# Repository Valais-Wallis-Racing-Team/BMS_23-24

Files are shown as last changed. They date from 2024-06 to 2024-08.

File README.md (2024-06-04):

# foxBMS

> **_NOTE:_**
> - This is the repository of the **first generation** of foxBMS
>   (https://github.com/foxBMS/foxbms)
> - The **second generation** of foxBMS (foxBMS 2) is also found on Github
>   (https://github.com/foxBMS/foxbms-2)

foxBMS is a free, open and flexible development environment to design battery
management systems. It is the first modular open source BMS development
platform.

## Documentation

A current build of the documentation of this project can be found
here:
- [latest documentation build (of the most recent release)](https://iisb-foxbms.iisb.fraunhofer.de/foxbms/gen1/docs/html/latest/)
- [list of all available documentation builds](https://iisb-foxbms.iisb.fraunhofer.de/foxbms/gen1/docs/html/)

## Changelog

The project changelog is found in
[CHANGELOG.rst](./CHANGELOG.rst).

## License

The license information of the project is found in [LICENSE.md](./LICENSE.md).

Basically, the software is covered by the
[**BSD 3-Clause License (SPDX short identifier: BSD-3-Clause)**](https://opensource.org/licenses/BSD-3-Clause)
and the hardware and documentation by the
[**Creative Commons Attribution 4.0 International License (SPDX short identifier: CC-BY-4.0)**](https://creativecommons.org/licenses/by/4.0/legalcode).

## Acknowledgment

For funding acknowledgements and instructions on how to acknowledge foxBMS
please see [foxbms.org/acknowledgements](https://foxbms.org/acknowledgements/).

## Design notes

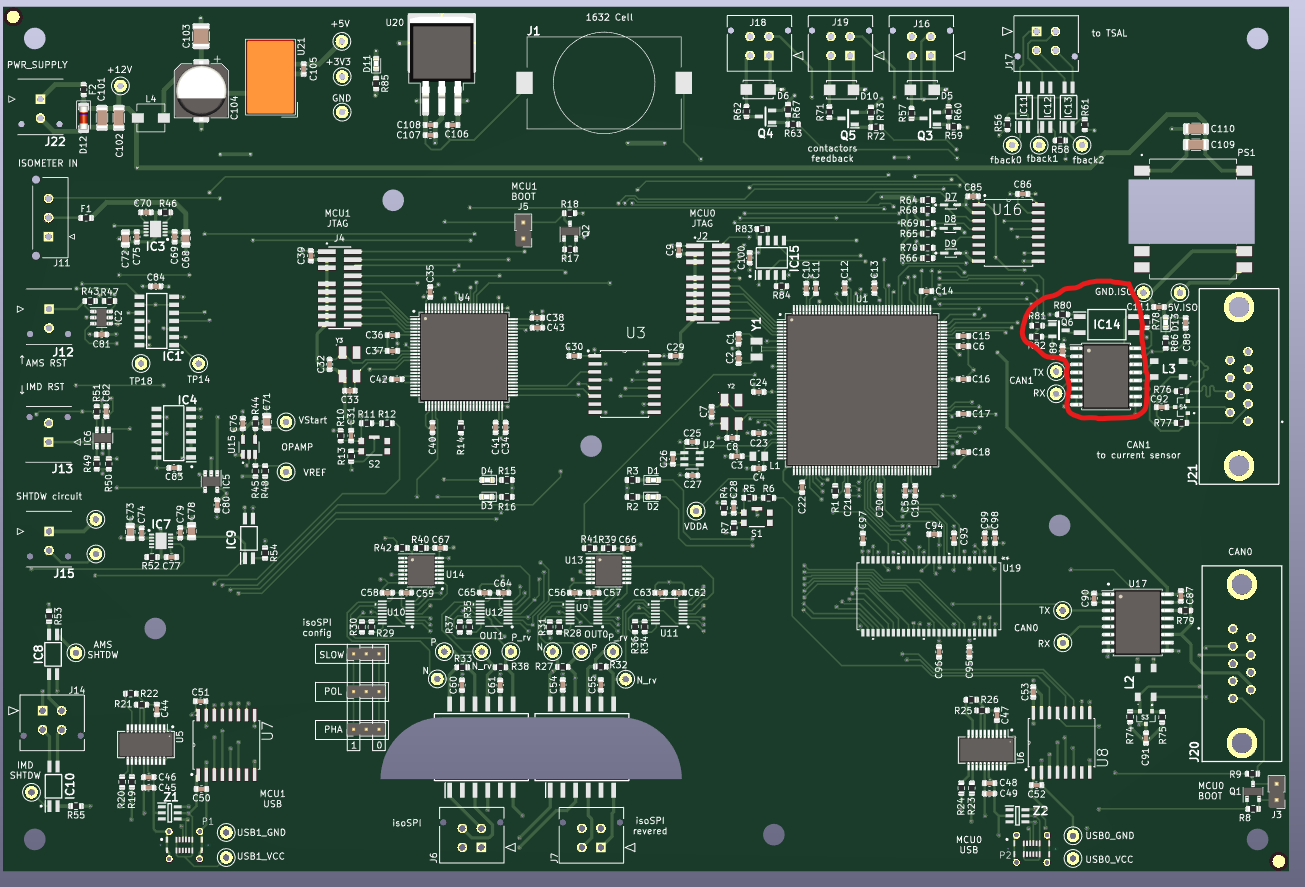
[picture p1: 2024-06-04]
hardware_KI_CAD/BMS-Master/BMS-MasterV1.1/BMS-Master_V1.0/conformal_coating_placement.png

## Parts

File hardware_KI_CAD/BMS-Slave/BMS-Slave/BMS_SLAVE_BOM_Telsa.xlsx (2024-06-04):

Fournisseur | Nbr. | N° article | Référence | Valeur | Empreinte | Description | Fitted (X) | Generic (X) | Through-hole (X) | prix unitaire | prix total
BOM BMS-Slave |  |  |  |  |  |  |  |  |  | Liste actualisée le : 12.01.2024
Composants électriques et électroniques
 | 12 | generic | C1-C3, C8-C10, C70-C72, C104-C106 | 1uF/50V | Capacitor_SMD:C_0805_2012Metric | Capa 1uF/50V | X | X |  |  | 0.00 CHF
 | 16 | generic | C4, C11, C17, C43, C53, C68, C73, C79, C107, C114, C116, C126, C139-C142 | 100nF/50V | Capacitor_SMD:C_0603_1608Metric | Capa 100nF/50V | X | X |  |  | 0.00 CHF
 | 4 | generic | C5, C12, C74, C108 | 100nF/200V | Capacitor_SMD:C_1206_3216Metric | Capa 100nF/200V | X | X |  |  | 0.00 CHF
 | 8 | generic | C6, C7, C13, C14, C75, C76, C109, C110 | 100pF/50V | Capacitor_SMD:C_0603_1608Metric | Capa 100pF/50V | X | X |  |  | 0.00 CHF
Mouser | 4 | 80-EDH336M100A9MAA | C15, C66, C77, C112 | 33uF/100V | Capacitor_SMD:CP_Elec_8x10 | Capa électrolitique 33uF/100V | X |  |  | 0.61 | 2.44 CHF
 | 4 | generic | C16, C67, C78, C113 | 2.2uF/100V | Capacitor_SMD:C_1210_3225Metric | Capa 2.2uF/100V | X | X |  |  | 0.00 CHF
 | 84 | generic | C18-C41, C44-C51, C54-C61, C64, C65, C80-C103, C117-C124, C127-C134, C137, C138 | 10nF/100V | Capacitor_SMD:C_0603_1608Metric | Capa 10nF/100V | X | X |  |  | 0.00 CHF
 | 12 | generic | C42, C52, C62, C63, C115, C125, C135, C136, C143-C146 | 1uF/50V | Capacitor_SMD:C_0603_1608Metric | Capa 1uF/50V | X | X |  |  | 0.00 CHF
 | 2 | generic | C69, C111 | 10nF/50V | Capacitor_SMD:C_0603_1608Metric | Capa 10nF/50V | X | X |  |  | 0.00 CHF
Mouser | 4 | 78-TLMG1100 | D1, D4, D20, D35 | LED Green TLMG1100-GS08 | LED_0603_1608Metric | Standard LEDs - SMD Green Non-Diffused | X |  |  | 0.31 | 1.24 CHF
Mouser | 4 | 621-DFLS1100-7 | D2, D5, D21, D36 | DFLS1100-7 | PowerDI123 | Schottky Diodes & Rectifiers 1.0A 100V | X |  |  | 0.29 | 1.16 CHF
Mouser | 4 | 625-SMAJ54A-E3 | D3, D6, D22, D37 | SMAJ54A-E3/61 | SMA | ESD Suppressors / TVS Diodes 400W 54V | X |  |  | 0.37 | 1.48 CHF
Mouser | 24 | 863-SZMMSZ4692T1G | D7-D18, D23-D34 | SZMMSZ4692T1G | SOD-123 | Zener Diodes ZEN REG 0.5W 6.8V | X |  |  | 0.35 | 8.40 CHF
Mouser | 2 | 771-BAT54C-T/R | D19, D38 | BAT54C,215 | SOT-23 | Schottky Diodes & Rectifiers BAT54C/SOT23/TO-236AB | X |  |  | 0.15 | 0.30 CHF
Mouser | 4 | 652-SF-0603SP063-2 | F1, F2, F18, F34 | SF-0603SP063-2 | Fuse_0603_1608Metric | Surface Mount Fuses .63A 32V TIME DELAY | X |  |  | 0.39 | 1.56 CHF
Mouser | 26 | 576-0466.250NR | F3-F5, F7-F9, F11-F17, F19-F21, F23-F25, F27-F33 | 0466.250NR | 0466.250NR:FUSC3215X66N | Surface Mount Fuses .25A 125V VERY FAST ACTING | X |  |  | 0.62 | 16.12 CHF
Mouser | 4 | 576-0448.500MR | F6, F10, F22, F26 | 0448.500MR | 0448_500MR:FUSC6127X294N | Surface Mount Fuses 125VAC 0.5A .38ohms 448 NANO2 | X |  |  | 1.16 | 4.64 CHF
Mouser | 4 | 511-M24M02-DWMN3TP/K | IC1, IC2, IC15, IC16 | M24M02-DWMN3TP_K | SO-8 | EEPROM Automotive 2-Mbit serial I2C bus EEPROM 1 MHz clock | X |  |  | 3.89 | 15.56 CHF
Mouser | 24 | 630-ACPL-217-56BE | IC3-IC14, IC17-IC28 | ACPL-217-56BE | SO-4 | Transistor Output Optocouplers 3000Vrms 50% CTR | X |  |  | 0.59 | 15.56 CHF
Mouser | 2 | 538-43045-0412 | J1, J2 | 430450412 | Molex_Micro-Fit_3.0_43045-0412_2x02_P3.00mm_Vertical | Molex micro-fit 3.0 4position 2 rows vertical | X |  | X | 0.94 | 14.16 CHF
Mouser | 4 | 538-430-45-0212 | J3, J7, J9, J13 | 43045-0212 | Molex_Micro-Fit_3.0_43650-0215_1x02_P3.00mm_Vertical | Molex micro-fit 3.0 2position 1row vertical | X |  | X | 0.75 | 1.88 CHF
Mouser | 4 | 538-43045-0612 | J4, J6, J10, J12 | 43045-0612 | Molex_Micro-Fit_3.0_43045-0612_2x03_P3.00mm_Vertical | Molex micro-fit 3.0 6position 2 rows vertical | X |  | X | 1.19 | 3.00 CHF
Mouser | 2 | 538-43045-1412 | J5, J11 | 43045-1412 | Molex_Micro-Fit_3.0_43045-1412_2x07_P3.00mm_Vertical | Molex micro-fit 3.0 14position 2 rows vertical | X |  | X | 2.59 | 4.76 CHF
Mouser | 2 | 538-43045-1612 | J8, J14 | 43045-1612 | Molex_Micro-Fit_3.0_43045-1612_2x08_P3.00mm_Vertical | Molex micro-fit 3.0 16position 2 rows vertical | X |  | X | 2.98 | 5.18 CHF
Mouser | 4 | 495-TCK-176 | L1-L4 | 4.7uH | TCK176 | Power Inductors - SMD 4.7uH 52mOhm 4.5A Inductor | X |  |  | 3.49 | 5.96 CHF
Mouser | 24 | 771-NX2301P215 | Q1-Q24 | NX2301P_215 (P-chanel MOSFET) | SOT23 | MOSFET NX2301P/SOT23 | X |  |  | 0.28 | 13.96 CHF
 | 44 | generic | R1, R10, R12, R21, R22, R37-R44, R53-R60, R119, R120, R129, R130, R145, R154, R204-R212, R221-R228 | 10k | Resistor_SMD:R_0603_1608Metric | Resistor SMD 10k 0603 | X | X |  |  | 6.72 CHF
 | 4 | generic | R2, R13, R121, R146 | 270R | Resistor_SMD:R_0603_1608Metric | Resistor SMD 270R 0603 | X | X |  |  | 0.00 CHF
 | 4 | generic | R3, R14, R122, R147 | 100R | Resistor_SMD:R_0805_2012Metric | Resistor SMD 100R 0803 | X | X |  |  | 0.00 CHF
 | 8 | generic | R4, R7, R15, R18, R123, R126, R148, R151 | 120R | Resistor_SMD:R_0603_1608Metric | Resistor SMD 120R 0603 | X | X |  |  | 0.00 CHF
 | 12 | generic | R5, R8, R9, R16, R19, R20, R124, R127, R128, R149, R152, R153 | 1k2 | Resistor_SMD:R_0603_1608Metric | Resistor SMD 1k2 0603 | X | X |  |  | 0.00 CHF
 | 4 | generic | R6, R17, R125, R150 | 820R | Resistor_SMD:R_0603_1608Metric | Resistor SMD 820R 0603 | X | X |  |  | 0.00 CHF
 | 4 | generic | R11, R23, R131, R155 | 1M | Resistor_SMD:R_0603_1608Metric | Resistor SMD 1M 0603 | X | X |  |  | 0.00 CHF
 | 62 | generic | R24-R36, R45-R52, R61-R70, R132-R144, R213-R220, R229-R238 | 100R | Resistor_SMD:R_0603_1608Metric | Resistor SMD 100R 0603 | X | X |  |  | 0.00 CHF
 | 24 | generic | R71, R72, R79, R80, R87, R88, R95-R97, R107-R109, R156, R157, R164, R165, R172, R173, R180-R182, R192-R194 | 3k3 | Resistor_SMD:R_0603_1608Metric | Resistor SMD 3k3 0603 | X | X |  |  | 0.00 CHF
 | 24 | generic | R73, R74, R81, R82, R89, R90, R98-R100, R110-R112, R158, R159, R166, R167, R174, R175, R183-R185, R195-R197 | 150R | Resistor_SMD:R_0603_1608Metric | Resistor SMD 150R 0603 | X | X |  |  | 0.00 CHF
 | 48 | generic | R75-R78, R83-R86, R91-R94, R101-R106, R113-R118, R160-R163, R168-R171, R176-R179, R186-R191, R198-R203 | 68R 1/3W | Resistor_SMD:R_2010_5025Metric | Resistor SMD 68R 2010 1/3W | X | X |  |  | 0.00 CHF
Farnell | 4 | 3861166 | T1-T4 | HM2102NL | SOP200P1473X500-12N | Common Mode Chokes / Filters MDL DUAL XFMR-CMC AEC-Q200 | X |  |  | 5.97 | 0.00 CHF
 | 16 |  | TP1-TP16 | TestPoint | TestPoint:TestPoint_Keystone_5000-5004_Miniature | test points |  |  | X |  | 23.88 CHF
Mouser | 4 | 584-LTC6811HG-1#PBF | U1, U2, U9, U11 | LTC6811HG-1_PBF | SOP50P780X200-48N | Battery Management 12 Channel Multicell Battery Monitor with Daisy Chain Interface, Generation 4 | X |  |  | 18.68 | 0.00 CHF
DigiKex | 4 | 1951-TSR0.6-4890WI-ND | U3, U8, U10, U12 | TSR 0.6-4890WI | TSR 0.6-4850WI | DC/DC converter 14V to 72V in 9V out | X |  | X | 9.34 | 74.72 CHF
Mouser | 4 | 584-ADG728BRUZ | U4, U5, U13, U14 | ADG728BRUZ | TSSOP-16_4.4x5mm_P0.65mm | Multiplexer Switch ICs SERIAL I2C, 8-ch MUX | X |  |  | 5.63 | 37.36 CHF
Mouser | 4 | 584-AD8628ARTZ-R2 | U6, U7, U15, U16 | AD8628ARTZ-R2 | SOT-23-5 | SP Amp Chopper Stabilization Single R-R I/O Â±2.5V/5V 5-Pin SOT-23 T/R | X |  |  | 4.01 | 22.52 CHF
Mouser | 4 | 926-LM1086ISX50NOPB | U17-U20 | LM1086ISX-5.0/NOPB | TO-263-3 | LDO Voltage Regulators 5V 1.5A LDO Positve Reg | X |  |  | 1.89
 |  |  |  |  |  | Prix total final : |  |  |  |  | 282.56 CHF

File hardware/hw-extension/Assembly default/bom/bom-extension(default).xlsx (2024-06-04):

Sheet: BOM
BOM for extension, Variant default
Generated on 26.10.2018 08:24:22
Line # | Designator | Quantity | Name | Description | Case EIA | Manufacturer 1 | Manufacturer Part Number 1 | Supplier 1 | Supplier Part Number 1 | MOQ | multiple | order quantity | Automotive Qualified
 | C801, C1102, C1301, C1502, C1703, C1902 | 6 | 1u/50V | MLCC | 0603 | Taiyo Yuden (https://octopart-clicks.com/click/altium?sku=2779055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) | UMK107AB7105KA-T (https://octopart-clicks.com/click/altium?sku=2779055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) | Farnell | 2779055 (https://octopart-clicks.com/click/altium?sku=2779055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) |  | 1 | 6
 | C802, C803, C805, C806, C807, C1101, C1103, C1104, C1105, C1106, C1302, C1303, C1304, C1305, C1306, C1501, C1701, C1702, C1704, C1705, C1706, C1707, C1708, C1901, C1903, C1904, C1905, C1906, C1907 | 29 | 100n/50V | MLCC | 0603 | Vishay (https://octopart-clicks.com/click/altium?sku=2525267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) | VJ0603Y104KXAAC31X (https://octopart-clicks.com/click/altium?sku=2525267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) | Farnell | 2525267 (https://octopart-clicks.com/click/altium?sku=2525267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) |  | 1 | 29
 | C804 | 1 | 4n7/50V | MLCC | 0603 | KEMET (https://octopart-clicks.com/click/altium?sku=2904754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) | C0603C472J5RACAUTO (https://octopart-clicks.com/click/altium?sku=2904754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) | Farnell | 2904754 (https://octopart-clicks.com/click/altium?sku=2904754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) |  | 1 | 1 | True
 | D801 | 1 | PESD1CAN | CAN Bus ESD Protection Diode, 200 W, 24 V, -65 to 150 degC, 3-Pin SOT23, RoHS, Tape and Reel |  | NXP Semiconductors | PESD1CAN |  |  |  | 1 | 1
 | D1101, D1102, D1103, D1901, D1902, D1903, D1904 | 7 | CDSOD323-T05 | TVS Diode, CDSOD323 Series, Unidirectional, 5 V, 18.3 V, SOD-323, 2 Pins |  | Bourns (https://octopart-clicks.com/click/altium?sku=2341914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) | CDSOD323-T05 (https://octopart-clicks.com/click/altium?sku=2341914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) | Farnell | 2341914 (https://octopart-clicks.com/click/altium?sku=2341914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) |  | 1 | 7
 | D1701, D1702, D1703, D1704, D1705 | 5 | MM3Z3V3ST1G | Zener Voltage Regulator, 300 mW, Tight Tolerance Portfolio, 2-Pin SOD-323, Pb-Free, Tape and Reel |  | ON Semiconductor | MM3Z3V3ST1G |  |  |  | 1 | 5
 | F1001, F1002, F1003 | 3 | Schurter SMD Fuse 4.0A UMT 3403.0172.11 | Schurter SMD Fuse 4.0A UMT 3403.0172.11 |  | Schurter (https://octopart-clicks.com/click/altium?sku=486-1253-ND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) | 3403.0172.11 (https://octopart-clicks.com/click/altium?sku=486-1253-ND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) | Digi-Key | 486-1253-ND (https://octopart-clicks.com/click/altium?sku=486-1253-ND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) |  | 1 | 3
 | IC801 | 1 | KA7805ERT | 3-Terminal 1 A Positive Voltage Regulator |  | ON Semiconductor / Fairchild (https://octopart-clicks.com/click/altium?manufacturer=ON%20Semiconductor%20%2F%20Fairchild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) | KA7805ERTF (https://octopart-clicks.com/click/altium?manufacturer=ON%20Semiconductor%20%2F%20Fairchild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) | Farnell | 2102585 (https://octopart-clicks.com/click/altium?manufacturer=ON%20Semiconductor%20%2F%20Fairchild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) |  | 1 | 1
 | IC802 | 1 | CPC1008N | Single-Pole, Normally Open 4-Pin SOP OptoMOS Relay |  | CPC (https://octopart-clicks.com/click/altium?sku=1653755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) | CPC1008N (https://octopart-clicks.com/click/altium?sku=1653755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) | Farnell | 1653755 (https://octopart-clicks.com/click/altium?sku=1653755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) |  | 1 | 1
 | IC803 | 1 | TJA1052IT/5Y | Galvanically Isolated High-Speed CAN Transceiver, -40 to 125 degC, 16-Pin SOIC, RoHS, Tape and Reel |  | NXP Semiconductors (https://octopart-clicks.com/click/altium?sku=2400552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) | TJA1052IT/5Y (https://octopart-clicks.com/click/altium?sku=2400552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) | Farnell | 2400552 (https://octopart-clicks.com/click/altium?sku=2400552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) |  | 1 | 1
 | IC1001, IC1002, IC1003, IC2001, IC2002, IC2003, IC2004, IC2005, IC2006 | 9 | AQV252G2SX | PhotoMOS Relay |  | Panasonic (https://octopart-clicks.com/click/altium?sku=2302216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) | AQV252G2SX (https://octopart-clicks.com/click/altium?sku=2302216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) | Farnell | 2302216 (https://octopart-clicks.com/click/altium?sku=2302216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) |  | 1 | 9
 | IC1101, IC1301, IC1901 | 3 | UA78L05CPK | Positive-Voltage Regulator, 100 mA, 0 to 125 degC, 3-Pin SOT-89 (PK), Green (RoHS & no Sb/Br), Tape and Reel |  | Texas Instruments (https://octopart-clicks.com/click/altium?sku=2112604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) | UA78L05CPK (https://octopart-clicks.com/click/altium?sku=2112604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) | Farnell | 2112604 (https://octopart-clicks.com/click/altium?sku=2112604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) |  | 1 | 3
 | IC1102 | 1 | ADUM3300CRWZ | Triple Channel Digital Isolator, Enhanced System-Level ESD Reliability, 2.5 KV rms Insulation Rating, 90 Mbps Data Rate, 32 ns Delay, Industrial, 16-pin SOIC (RW-16), Tube |  | Analog Devices (https://octopart-clicks.com/click/altium?sku=584-ADUM3300CRWZ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) | ADUM3300CRWZ (https://octopart-clicks.com/click/altium?sku=584-ADUM3300CRWZ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) | Mouser | 584-ADUM3300CRWZ (https://octopart-clicks.com/click/altium?sku=584-ADUM3300CRWZ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) |  | 1 | 1
 | IC1302 | 1 | LT1785 | Transceiver RS422/RS485, Fault Protected, 4.75V-5.25V supply, SOIC-8 |  | Analog Devices / Linear Technology (https://octopart-clicks.com/click/altium?sku=1663498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) | LT1785CS8#PBF (https://octopart-clicks.com/click/altium?sku=1663498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) | Farnell | 1663498 (https://octopart-clicks.com/click/altium?sku=1663498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) |  | 1 | 1
 | IC1303 | 1 | ADUM3401CRWZ | Quad Channel Digital Isolator, Enhanced System-Level ESD Reliability, 2.5 KV rms Insulation Rating, 90 Mbps Data Rate, 32 ns Delay, Industrial, 16-pin SOIC (RW-16), Tube |  | Analog Devices (https://octopart-clicks.com/click/altium?sku=1274129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) | ADUM3401CRWZ (https://octopart-clicks.com/click/altium?sku=1274129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) | Farnell | 1274129 (https://octopart-clicks.com/click/altium?sku=1274129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) |  | 1 | 1
 | IC1701 | 1 | ADR3425ARJZ-R2 | Micropower, High Accuracy Voltage Reference, 2.5 V Output, 2.7 to 5.5 V Supply, Industrial, 6-pin SOT23 (RJ-6), Reel |  | Analog Devices (https://octopart-clicks.com/click/altium?sku=2377039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) | ADR3425ARJZ-R2 (https://octopart-clicks.com/click/altium?sku=2377039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) | Farnell | 2377039 (https://octopart-clicks.com/click/altium?sku=2377039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) |  | 1 | 1
 | IC1902, IC1903 | 2 | ADUM3402BRWZ | Quad Channel Digital Isolator, Enhanced System-Level ESD Reliability, 2.5 KV rms Insulation Rating, 10 Mbps Data Rate, 50 ns Delay, Industrial, 16-pin SOIC (RW-16), Tube |  | Analog Devices (https://octopart-clicks.com/click/altium?sku=1274127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) | ADUM3402BRWZ (https://octopart-clicks.com/click/altium?sku=1274127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) | Farnell | 1274127 (https://octopart-clicks.com/click/altium?sku=1274127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) |  | 1 | 2
 | JP2201, JP2202 | 2 | X2x12 | Board-To-Board Connector, Vertical, Low Profile, 2.54 mm, 24 Contacts, Header, TLW Series, Through Hole, 2 Rows |  | Samtec (https://octopart-clicks.com/click/altium?sku=SAM1096-12-ND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) | TLW-112-06-G-D (https://octopart-clicks.com/click/altium?sku=SAM1096-12-ND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) | Digikey | SAM1096-12-ND (https://octopart-clicks.com/click/altium?sku=SAM1096-12-ND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) |  | 1 | 2
 | L801 | 1 | 51uH | Common Mode Choke |  | TDK EPCOS (https://octopart-clicks.com/click/altium?sku=871-B82789C0513H002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) | B82789C0513H002 (https://octopart-clicks.com/click/altium?sku=871-B82789C0513H002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) | Mouser | 871-B82789C0513H002 (https://octopart-clicks.com/click/altium?sku=871-B82789C0513H002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) |  | 1 | 1
 | L1501 | 1 | BLM21AG471SN1J | Chip Ferrite Bead for General Signal lines, 470 Ohm, 700 mA, -55 to 125 degC, 2 x 1.25 x 1.05 mm SMD, Tape and Reel |  | Laird (https://octopart-clicks.com/click/altium?sku=2292413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) | HZ0805G471R-10 (https://octopart-clicks.com/click/altium?sku=2292413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) | Farnell | 2292413 (https://octopart-clicks.com/click/altium?sku=2292413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) |  | 1 | 1
 | R801, R802 | 2 | 62R | SMD Resistor 62R 0603 | 0603 | Multicomp (https://octopart-clicks.com/click/altium?sku=2073943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) | MCMR12X62R0FTL (https://octopart-clicks.com/click/altium?sku=2073943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) | Farnell | 2073943 (https://octopart-clicks.com/click/altium?sku=2073943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) |  | 1 | 2
 | R803, R805, R901, R1002, R1005, R1008, R1104, R1105, R1106, R1502, R1503, R1504, R1505, R1506, R1507, R1903, R1904, R1907, R1908, R2003, R2004, R2009, R2010, R2015, R2016 | 25 | 10k | SMD Resistor 10k 0603 | 0603 | Multicomp (https://octopart-clicks.com/click/altium?sku=2073349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) | MCMR06X1002FTL (https://octopart-clicks.com/click/altium?sku=2073349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) | Farnell | 2073349 (https://octopart-clicks.com/click/altium?sku=2073349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) |  | 1 | 25
 | R804, R1003, R1006, R1009, R2005, R2006, R2011, R2012, R2017, R2018 | 10 | 430R | SMD Resistor 430R 0603 | 0603 | Multicomp (https://octopart-clicks.com/click/altium?sku=2074259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) | MCSR06X4300FTL (https://octopart-clicks.com/click/altium?sku=2074259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) | Farnell | 2074259 (https://octopart-clicks.com/click/altium?sku=2074259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) |  | 1 | 10
 | R806, R902, R1001, R1004, R1007, R2001, R2002, R2007, R2008, R2013, R2014 | 11 | 10R | SMD Resistor 10R 0603 | 0603 | Multicomp (https://octopart-clicks.com/click/altium?sku=2073361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) | MCMR06X10R0FTL (https://octopart-clicks.com/click/altium?sku=2073361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) | Farnell | 2073361 (https://octopart-clicks.com/click/altium?sku=2073361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) |  | 1 | 11
 | R1101, R1102, R1103, R1901, R1902, R1905, R1906 | 7 | 47R | SMD Resistor 47R 0603 | 0603 | Panasonic (https://octopart-clicks.com/click/altium?sku=2303030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) | ERJ-3EKF47R0V (https://octopart-clicks.com/click/altium?sku=2303030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) | Farnell | 2303030 (https://octopart-clicks.com/click/altium?sku=2303030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) |  | 1 | 7
 | R1501 | 1 | 47k | SMD Resistor 47k 0603 | 0603 | Multicomp (https://octopart-clicks.com/click/altium?sku=2073510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) | MCMR06X4702FTL (https://octopart-clicks.com/click/altium?sku=2073510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) | Farnell | 2073510 (https://octopart-clicks.com/click/altium?sku=2073510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) |  | 1 | 1
 | R1701, R1703, R1705, R1707, R1709 | 5 | 0R | SMD Resistor 0R 0603 | 0603 | Multicomp (https://octopart-clicks.com/click/altium?sku=2073345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) | MCMR06X000PTL (https://octopart-clicks.com/click/altium?sku=2073345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) | Farnell | 2073345 (https://octopart-clicks.com/click/altium?sku=2073345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) |  | 1 | 5
 | R1702, R1704, R1706, R1708, R1710 | 5 | 4k75 | SMD Resistor 4k75 0603 | 0603 | Multicomp (https://octopart-clicks.com/click/altium?sku=2073517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) | MCMR06X4751FTL (https://octopart-clicks.com/click/altium?sku=2073517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) | Farnell | 2073517 (https://octopart-clicks.com/click/altium?sku=2073517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) |  | 1 | 5
 | SLOT1501 | 1 | MOLEX_47352-1001 | 1.10mm Pitch Memorycard Card Connector, Push-Push Type, with VSS (Supply Voltage Ground) Detect Switch, Lead-Free |  | Molex (https://octopart-clicks.com/click/altium?sku=2424133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) | 47352-1001 (https://octopart-clicks.com/click/altium?sku=2424133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) | Farnell | 2424133 (https://octopart-clicks.com/click/altium?sku=2424133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) |  | 1 | 1 | False
 | SV901 | 1 | samtec_TLW-104-06-G-D | Board-To-Board Connector, Vertical, Low Profile, 2.54 mm, 8 Contacts, Header, TLW Series, Through Hole, 2 Rows |  | Samtec (https://octopart-clicks.com/click/altium?sku=SAM1096-04-ND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) | TLW-104-06-G-D (https://octopart-clicks.com/click/altium?sku=SAM1096-04-ND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) | Digikey | SAM1096-04-ND (https://octopart-clicks.com/click/altium?sku=SAM1096-04-ND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) |  | 1 | 1
 | T801, T1001, T1002, T1003, T2001, T2002, T2003, T2004, T2005, T2006 | 10 | IRLML0100TRPBF | MOSFET-Transistor, n-Kanal, 1.6 A, 100 V, 0.178 ohm, 10 V, 2.5 V |  | International Rectifier (https://octopart-clicks.com/click/altium?sku=1783928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) | IRLML0100TRPBF (https://octopart-clicks.com/click/altium?sku=1783928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) | Farnell | 1783928 (https://octopart-clicks.com/click/altium?sku=1783928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) |  | 1 | 10
 | T901 | 1 | BUK964R8-60E,118 | N-Channel TrenchMOS Logic Level FET, 60 V, 100 A, 3-Pin SOT404, Tape and Reel |  | NXP Semiconductors (https://octopart-clicks.com/click/altium?manufacturer=NXP%20Semiconductors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) | BUK964R8-60E,118 (https://octopart-clicks.com/click/altium?manufacturer=NXP%20Semiconductors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) | Digi-Key | 1727-7261-6-ND (https://octopart-clicks.com/click/altium?manufacturer=NXP%20Semiconductors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) |  | 1 | 1 | Y
 | T1501 | 1 | BSS84P | P-Channel SIPMOS Small-Signal-Transistor, -60 V VDS, -0.17 A ID, -55 to 150 degC, PG-SOT23, Reel, Green |  | Infineon | BSS84P |  |  |  | 1 | 1
 | X801, X1201, X1202, X1203 | 4 | molex_microfit_3_02x2_THT | Micro-Fit 3.0 Right Angle Header, 3.00mm Pitch, Dual Row, 4 Circuits, with Snap-in Plastic Peg PCB Lock, Tin, Glow Wire Capable, Black, 43045-0400 |  | Molex (https://octopart-clicks.com/click/altium?sku=9733019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) | 43045-0400 (https://octopart-clicks.com/click/altium?sku=9733019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) | Farnell | 9733019 (https://octopart-clicks.com/click/altium?sku=9733019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) |  | 1 | 4
 | X1301 | 1 | molex_microfit_3_03x2_THT | Micro-Fit 3.0 Right Angle Header, 3.00mm Pitch, Dual Row, 6 Circuits, with Snap-in Plastic Peg PCB Lock, Tin, Glow Wire Capable, Black, 43045-0600 |  | Molex (https://octopart-clicks.com/click/altium?sku=1012252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) | 43045-0600 (https://octopart-clicks.com/click/altium?sku=1012252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) | Farnell | 1012252 (https://octopart-clicks.com/click/altium?sku=1012252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) |  | 1 | 1
 | X1701, X2001 | 2 | molex_microfit_3_06x2_THT | Micro-Fit 3.0 Right Angle Header, 3.00mm Pitch, Dual Row, 12 Circuits, with Snap-in Plastic Peg PCB Lock, Tin, Glow Wire Capable, Black, 43045-1200 |  | Molex (https://octopart-clicks.com/click/altium?sku=9732977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) | 43045-1200 (https://octopart-clicks.com/click/altium?sku=9732977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) | Farnell | 9732977 (https://octopart-clicks.com/click/altium?sku=9732977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) |  | 1 | 2
 | X1901 | 1 | molex_microfit_3_05x2_THT | Micro-Fit 3.0 Right Angle Header, 3.00mm Pitch, Dual Row, 10 Circuits, with Snap-in Plastic Peg PCB Lock, Tin, Glow Wire Capable, Black, 43045-1000 |  | Molex (https://octopart-clicks.com/click/altium?sku=1012255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) | 43045-1000 (https://octopart-clicks.com/click/altium?sku=1012255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) | Farnell | 1012255 (https://octopart-clicks.com/click/altium?sku=1012255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) |  | 1 | 1

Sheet: DATA
extension.PrjPcb
26.10.2018 08:24:22
default

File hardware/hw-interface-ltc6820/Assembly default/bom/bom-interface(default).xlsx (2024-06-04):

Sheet: BOM
BOM for interface, Variant default
Generated on 15.03.2019 09:42:01
Line # | Designator | Quantity | Name | Description | #Column Name Error:Case EIA | Manufacturer 1 | Manufacturer Part Number 1 | Supplier 1 | Supplier Part Number 1
1 | JP203_1, JP203_2, JP204_1, JP204_2, JP205_1, JP205_2, JP206_1, JP206_2, R203_1, R203_2 | 10 | 0R | SMD Resistor 0R 0603 |  | Vishay Semiconductors (https://octopart-clicks.com/click/altium?sku=2616580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) | RCA06030000ZSEA (https://octopart-clicks.com/click/altium?sku=2616580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) | Farnell | 2616580 (https://octopart-clicks.com/click/altium?sku=2616580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)
2 | R400_1, R400_2, R401_1, R401_2 | 4 | 120R | SMD Resistor 120R 0603 |  | Vishay (https://octopart-clicks.com/click/altium?sku=1652832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) | CRCW0603120RFKEA (https://octopart-clicks.com/click/altium?sku=1652832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) | Farnell | 1652832 (https://octopart-clicks.com/click/altium?sku=1652832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)
3 | R250_1, R250_2, R250_3, R250_4 | 4 | 806R | SMD Resistor 806R 0603 |  | Panasonic (https://octopart-clicks.com/click/altium?sku=2059324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) | ERJ3EKF8060V (https://octopart-clicks.com/click/altium?sku=2059324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) | Farnell | 2059324 (https://octopart-clicks.com/click/altium?sku=2059324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)
4 | R251_1, R251_2, R251_3, R251_4 | 4 | 1k2 | SMD Resistor 1k2 0603 |  | Multicomp (https://octopart-clicks.com/click/altium?sku=2073370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) | MCMR06X1201FTL (https://octopart-clicks.com/click/altium?sku=2073370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) | Farnell | 2073370 (https://octopart-clicks.com/click/altium?sku=2073370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)
5 | R200_1, R200_2, R201_1, R201_2 | 4 | 2k | SMD Resistor 2k 0603 |  | Panasonic (https://octopart-clicks.com/click/altium?sku=2059343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) | ERJ3EKF2001V (https://octopart-clicks.com/click/altium?sku=2059343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) | Farnell | 2059343 (https://octopart-clicks.com/click/altium?sku=2059343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)
6 | R202_1, R202_2 | 2 | 20k | SMD Resistor 20k 0603 |  | Panasonic (https://octopart-clicks.com/click/altium?sku=2059432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) | ERJ3EKF2002V (https://octopart-clicks.com/click/altium?sku=2059432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) | Farnell | 2059432 (https://octopart-clicks.com/click/altium?sku=2059432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)
7 | C400_1, C400_2, C401_1, C401_2 | 4 | 27p/50V | MLCC |  | KEMET (https://octopart-clicks.com/click/altium?sku=2219430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) | C0603X270J5GACAUTO (https://octopart-clicks.com/click/altium?sku=2219430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) | Farnell | 2219430 (https://octopart-clicks.com/click/altium?sku=2219430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)
8 | C200_1, C200_2, C250_1, C250_2, C250_3, C250_4, C251_1, C251_2, C251_3, C251_4 | 10 | 100n/50V | MLCC |  | Vishay (https://octopart-clicks.com/click/altium?sku=2525267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) | VJ0603Y104KXAAC31X (https://octopart-clicks.com/click/altium?sku=2525267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) | Farnell | 2525267 (https://octopart-clicks.com/click/altium?sku=2525267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)
9 | IC250_1, IC250_2, IC250_3, IC250_4 | 4 | LTC6820HMS#PBF | IsoSPI Isolated Communication Interface, 2.7 to 5.5 V, -40 to 125 degC, 16-Pin MSOP (MS), Pb-Free |  | Analog Devices / Linear Technology (https://octopart-clicks.com/click/altium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) | LTC6820HMS#PBF (https://octopart-clicks.com/click/altium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) | Digi-Key | LTC6820HMS#PBF-ND (https://octopart-clicks.com/click/altium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)
10 | U200_1, U200_2 | 2 | SN74LVC00APWR | Quadruple 2-Input Positive-NAND Gate, PW0014A, LARGE T&R |  | Texas Instruments (https://octopart-clicks.com/click/altium?sku=1105931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) | SN74LVC00APWR (https://octopart-clicks.com/click/altium?sku=1105931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) | Farnell | 1105931 (https://octopart-clicks.com/click/altium?sku=1105931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)
11 | TR400_1, TR400_2 | 2 | HM2102NL | Pulse HM2102NL BMS Transformer |  | Pulse Electronics Network (https://octopart-clicks.com/click/altium?manufacturer=Pulse%20Electronics%20Network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) | HM2102NLT (https://octopart-clicks.com/click/altium?manufacturer=Pulse%20Electronics%20Network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) | Digi-Key | 1840-1034-1-ND (https://octopart-clicks.com/click/altium?manufacturer=Pulse%20Electronics%20Network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)
12 | J500, J501 | 2 | TE_534206-4 | Board-To-Board Connector, Dual, 2.54 mm, 8 Contacts, Receptacle, Through Hole, 2 Rows |  | TE Connectivity (https://octopart-clicks.com/click/altium?sku=A26454-ND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) | 534206-4 (https://octopart-clicks.com/click/altium?sku=A26454-ND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) | Digikey | A26454-ND (https://octopart-clicks.com/click/altium?sku=A26454-ND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)
13 | J300_1, J300_2 | 2 | SSW-108-01-G-D | SQ Post Socket, Through-hole, Vertical, -55 to 125 degC, 2.54mm Pitch, 16-Pin, Female, RoHS |  | Samtec (https://octopart-clicks.com/click/altium?sku=1668362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) | SSW-108-01-G-D (https://octopart-clicks.com/click/altium?sku=1668362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) | Farnell | 1668362 (https://octopart-clicks.com/click/altium?sku=1668362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)

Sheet: DATA
interface.PrjPcb
15.03.2019 09:42:01
default

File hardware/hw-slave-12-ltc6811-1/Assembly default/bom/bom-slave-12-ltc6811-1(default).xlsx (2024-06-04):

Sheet: BOM
BOM for slave-12-ltc6811-1, Variant default
Generated on 28.03.2019 11:59:38
Line # | Designator | Quantity | Name | Description | Case EIA | Manufacturer 1 | Manufacturer Part Number 1 | Supplier 1 | Supplier Part Number 1
 | IC800-1, IC800-2 | 2 | M24M02-DWMN3TP/K | Automotive 2-Mbit serial I²C bus EEPROM with 1 MHz clock |  | STMicroelectronics (https://octopart-clicks.com/click/altium?manufacturer=STMicroelectronics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) | M24M02-DWMN3TP/K (https://octopart-clicks.com/click/altium?manufacturer=STMicroelectronics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) | Digi-Key | 497-16238-1-ND (https://octopart-clicks.com/click/altium?manufacturer=STMicroelectronics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)
1 | R605-1, R605-2, R1402-1, R1403-2, R1406-1, R1407-2, R1410-1, R1410-2, R1413-1, R1413-2, R1417-1, R1417-2, R1419-2, R1420-1 | 14 | 0R | SMD Resistor 0R 0603 | 0603 | Vishay Semiconductors (https://octopart-clicks.com/click/altium?manufacturer=Vishay%20Semiconductors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) | RCA06030000ZSEA (https://octopart-clicks.com/click/altium?manufacturer=Vishay%20Semiconductors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) | Farnell | 2616580, 2073345 (https://octopart-clicks.com/click/altium?manufacturer=Vishay%20Semiconductors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)
2 | R108-1, R108-2, R109-1, R109-2, R110-1, R110-2, R111-1, R111-2, R112-1, R112-2, R113-1, R113-2, R114-1, R114-2, R115-1, R115-2, R116-1, R116-2, R118-1, R118-2, R1300-1, R1300-2, R1301-1, R1301-2, R1302-1, R1302-2, R1303-1, R1303-2, R1304-1, R1304-2, R1305-1, R1305-2, R1306-1, R1306-2, R1307-1, R1307-2, R1308-1, R1308-2, R1309-1, R1309-2, R1310-1, R1310-2, R1311-1, R1311-2, R1312-1, R1312-2 | 46 | 100R | SMD Resistor 100R 0603 | 0603 | Panasonic (https://octopart-clicks.com/click/altium?manufacturer=Panasonic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) | ERJ-3EKF1000V (https://octopart-clicks.com/click/altium?manufacturer=Panasonic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) | Digikey, Farnell | P100HCT-ND, 1469752 (https://octopart-clicks.com/click/altium?manufacturer=Panasonic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)
3 | R1422-1, R1422-2, R1423-1, R1423-2 | 4 | 120R | SMD Resistor 120R 0603 | 0603 | Multicomp (https://octopart-clicks.com/click/altium?sku=2073369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) | MCMR06X1200FTL (https://octopart-clicks.com/click/altium?sku=2073369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) | Farnell | 2073369 (https://octopart-clicks.com/click/altium?sku=2073369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)
4 | R1100, R1101, R1102, R1103, R1104, R1105, R1106, R1107, R1108, R1109, R1110, R1111 | 12 | 150R | SMD Resistor 150R 0603 | 0603 | Vishay (https://octopart-clicks.com/click/altium?sku=1469760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) | CRCW0603150RFKEA (https://octopart-clicks.com/click/altium?sku=1469760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) | Farnell | 1469760 (https://octopart-clicks.com/click/altium?sku=1469760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)
5 | R1406-2, R1407-1 | 2 | 270R | SMD Resistor 270R 0603 | 0603 | Vishay (https://octopart-clicks.com/click/altium?sku=2141320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) | CRCW0603270RFKEA (https://octopart-clicks.com/click/altium?sku=2141320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) | Farnell | 2141320 (https://octopart-clicks.com/click/altium?sku=2141320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)
6 | R1421-1, R1421-2 | 2 | 820R | SMD Resistor 820R 0603 | 0603 | Vishay (https://octopart-clicks.com/click/altium?sku=1469841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) | CRCW0603820RFKEA (https://octopart-clicks.com/click/altium?sku=1469841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) | Farnell | 1469841 (https://octopart-clicks.com/click/altium?sku=1469841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)
7 | R610-1, R610-2 | 2 | 1k | SMD Resistor 1k 0603 | 0603 | Vishay Dale (https://octopart-clicks.com/click/altium?sku=1652848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) | CRCW06031K00FKTA (https://octopart-clicks.com/click/altium?sku=1652848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) | Farnell | 1652848 (https://octopart-clicks.com/click/altium?sku=1652848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)
8 | R1415-1, R1415-2, R1416-1, R1416-2, R1419-1, R1420-2 | 6 | 1k21 | SMD Resistor 1k21 0603 | 0603 | Vishay (https://octopart-clicks.com/click/altium?sku=1652852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) | CRCW06031K21FKEA (https://octopart-clicks.com/click/altium?sku=1652852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) | Farnell | 1652852 (https://octopart-clicks.com/click/altium?sku=1652852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)
9 | R606-1, R606-2 | 2 | 1k5 | SMD Resistor 1k5 0603 | 0603 | Vishay Dale (https://octopart-clicks.com/click/altium?sku=2616745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) | CRCW06031K50JNEA (https://octopart-clicks.com/click/altium?sku=2616745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) | Farnell | 2616745 (https://octopart-clicks.com/click/altium?sku=2616745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)
10 | R603-1, R603-2, R608-1, R608-2 | 4 | 124k | SMD Resistor 124k 0603 | 0603 | Vishay (https://octopart-clicks.com/click/altium?sku=2138508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) | CRCW0603124KFKEA (https://octopart-clicks.com/click/altium?sku=2138508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) | Farnell | 2138508 (https://octopart-clicks.com/click/altium?sku=2138508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)
11 | R1500, R1501, R1506, R1507, R1512, R1513, R1518, R1519, R1524, R1525, R1530, R1531 | 12 | 3k3 | SMD Resistor 3k3 0603 | 0603 | Vishay (https://octopart-clicks.com/click/altium?sku=1469793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) | CRCW06033K30FKEA (https://octopart-clicks.com/click/altium?sku=1469793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) | Farnell | 1469793 (https://octopart-clicks.com/click/altium?sku=1469793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)
12 | R100-1, R100-2, R101-1, R101-2, R102-1, R102-2, R103-1, R103-2, R104-1, R104-2, R105-1, R105-2, R106-1, R106-2, R107-1, R107-2, R600-1, R600-2, R604-1, R604-2, R609-1, R609-2, R700-1, R700-2, R701-1, R701-2, R702-1, R702-2, R703-1, R703-2, R704-1, R704-2, R705-1, R705-2, R706-1, R706-2, R707-1, R707-2, R708-1, R708-2, R801-1, R801-2, R904, R1112, R1404-1, R1404-2, R1408-1, R1408-2, R1411-1, R1411-2 | 50 | 10k | SMD Resistor 10k 0603 | 0603 | Multicomp (https://octopart-clicks.com/click/altium?sku=2073349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) | MCMR06X1002FTL (https://octopart-clicks.com/click/altium?sku=2073349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) | Farnell | 2073349 (https://octopart-clicks.com/click/altium?sku=2073349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)
13 | R905 | 1 | 86k6 | SMD Resistor 86k6 0603 | 0603 | Panasonic (https://octopart-clicks.com/click/altium?sku=2059490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) | ERJ-3EKF8662V (https://octopart-clicks.com/click/altium?sku=2059490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) | Farnell | 2059490 (https://octopart-clicks.com/click/altium?sku=2059490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)
14 | R602-1, R602-2 | 2 | 68k | SMD Resistor 68k 0603 | 0603
15 | R902 | 1 | 150k | SMD Resistor 150k 0603 | 0603
16 | R901 | 1 | 390k | SMD Resistor 390k 0603 | 0603 | Panasonic (https://octopart-clicks.com/click/altium?sku=2303278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) | ERJ3EKF3903V (https://octopart-clicks.com/click/altium?sku=2303278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) | Farnell | 2303278 (https://octopart-clicks.com/click/altium?sku=2303278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)
17 | R1400-2, R1401-1 | 2 | 1M | SMD Resistor 1M 0603 | 0603 | Vishay (https://octopart-clicks.com/click/altium?sku=1469746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) | CRCW06031M00FKEA (https://octopart-clicks.com/click/altium?sku=1469746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) | Farnell | 1469746 (https://octopart-clicks.com/click/altium?sku=1469746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)
18 | R607-1, R607-2 | 2 | 1R | SMD Resistor 1R 0805 | 0805 | Vishay Dale (https://octopart-clicks.com/click/altium?sku=2616757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) | CRCW08051R00FKEA (https://octopart-clicks.com/click/altium?sku=2616757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) | Farnell | 2616757 (https://octopart-clicks.com/click/altium?sku=2616757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)
19 | R900 | 1 | 39R | SMD Resistor 39R 0805 | 0805 | Panasonic (https://octopart-clicks.com/click/altium?sku=1750736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) | ERJP06F39R0V (https://octopart-clicks.com/click/altium?sku=1750736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) | Farnell | 1750736 (https://octopart-clicks.com/click/altium?sku=1750736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)
20 | R1400-1, R1401-2 | 2 | 100R | SMD Resistor 100R 0805 | 0805 | Vishay Dale (https://octopart-clicks.com/click/altium?sku=1469862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) | CRCW0805100RFKEA (https://octopart-clicks.com/click/altium?sku=1469862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) | Farnell | 1469862 (https://octopart-clicks.com/click/altium?sku=1469862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)
21 | R1502, R1503, R1504, R1505, R1508, R1509, R1510, R1511, R1514, R1515, R1516, R1517, R1520, R1521, R1522, R1523, R1526, R1527, R1528, R1529, R1532, R1533, R1534, R1535 | 24 | 68R | SMD Resistor 68R 2010 | 2010 | Panasonic (https://octopart-clicks.com/click/altium?sku=2323988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) | ERJ-12ZYJ680U (https://octopart-clicks.com/click/altium?sku=2323988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) | Farnell | 2323988 (https://octopart-clicks.com/click/altium?sku=2323988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)
22 | C1404-1, C1404-2, C1405-1, C1405-2 | 4 | 100p/50V | MLCC | 0603 | KEMET (https://octopart-clicks.com/click/altium?sku=1414603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) | C0603C101J5GACTU (https://octopart-clicks.com/click/altium?sku=1414603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) | Farnell | 1414603 (https://octopart-clicks.com/click/altium?sku=1414603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)
23 | C102-1, C102-2, C103-1, C103-2, C104-1, C104-2, C105-1, C105-2, C106-1, C106-2, C107-1, C107-2, C108-1, C108-2, C109-1, C109-2, C111-1, C111-2, C115-1, C115-2, C600-1, C600-2, C1300-1, C1300-2, C1301-1, C1301-2, C1304-1, C1304-2, C1305-1, C1305-2, C1308-1, C1308-2, C1309-1, C1309-2, C1312-1, C1312-2, C1313-1, C1313-2, C1316-1, C1316-2, C1317-1, C1317-2, C1320-1, C1320-2, C1321-1, C1321-2 | 46 | 10n/100V | MLCC | 0603 | KEMET (https://octopart-clicks.com/click/altium?sku=1301715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) | C0603X103K1RACAUTO (https://octopart-clicks.com/click/altium?sku=1301715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) | Farnell | 1301715 (https://octopart-clicks.com/click/altium?sku=1301715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)
24 | C100-1, C100-2, C400, C401, C402, C403, C404, C405, C406, C407, C601-1, C601-2, C604-1, C604-2, C605-1, C605-2, C700-1, C700-2, C701-1, C701-2, C800-1, C800-2, C801-1, C801-2, C906, C1100 | 26 | 100n/50V | MLCC | 0603 | Murata (https://octopart-clicks.com/click/altium?sku=490-6049-1-ND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) | GCM188L81H104KA57D (https://octopart-clicks.com/click/altium?sku=490-6049-1-ND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) | Digi-Key | 490-6049-1-ND (https://octopart-clicks.com/click/altium?sku=490-6049-1-ND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)
25 | C902 | 1 | 470p/100V | MLCC | 0805 | Multicomp (https://octopart-clicks.com/click/altium?sku=1759283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) | MC0805B471K101CT (https://octopart-clicks.com/click/altium?sku=1759283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) | Farnell | 1759283 (https://octopart-clicks.com/click/altium?sku=1759283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)
27 | C101-1, C101-2, C110-1, C110-2, C112-1, C112-2, C113-1, C113-2, C114-1, C114-2, C606-1, C606-2, C904, C907, C1401-1, C1401-2, C1402-1, C1402-2, C1403-1, C1403-2 | 20 | 1u/35V | MLCC | 0603 | Murata (https://octopart-clicks.com/click/altium?sku=1907508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) | GRM188R7YA105KA12D (https://octopart-clicks.com/click/altium?sku=1907508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) | Farnell | 1907508 (https://octopart-clicks.com/click/altium?sku=1907508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)
28 | C607-1, C607-2, C608-1, C608-2 | 4 | 2u2/10V | MLCC | 0805 | KEMET (https://octopart-clicks.com/click/altium?sku=2478259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) | C0805C225K8RACAUTO (https://octopart-clicks.com/click/altium?sku=2478259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) | Farnell | 2478259 (https://octopart-clicks.com/click/altium?sku=2478259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)
29 | C603-1, C603-2, C1400-1, C1400-2 | 4 | 100n/100V | MLCC | 0805 | Multicomp (https://octopart-clicks.com/click/altium?sku=2320821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) | MC0805B104K101CT (https://octopart-clicks.com/click/altium?sku=2320821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) | Farnell | 2320821 (https://octopart-clicks.com/click/altium?sku=2320821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)
30 | C900, C901 | 2 | 2u2/250V | MLCC | 2220 | TDK (https://octopart-clicks.com/click/altium?sku=445-7997-2-ND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) | CGA9P3X7T2E225M250KE (https://octopart-clicks.com/click/altium?sku=445-7997-2-ND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) | Digi-Key | 445-7997-2-ND (https://octopart-clicks.com/click/altium?sku=445-7997-2-ND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)
32 | C903 | 1 | 4n7/1000V | MLCC | 1812 | KEMET (https://octopart-clicks.com/click/altium?sku=1702159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) | C1812C472KDRACTU (https://octopart-clicks.com/click/altium?sku=1702159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) | Farnell | 1702159 (https://octopart-clicks.com/click/altium?sku=1702159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)
33 | C602-1, C602-2 | 2 | 1u/250V | MLCC | 1812 | TDK (https://octopart-clicks.com/click/altium?sku=2435499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) | CGA8P3X7T2E105K250KA (https://octopart-clicks.com/click/altium?sku=2435499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) | Farnell | 2435499 (https://octopart-clicks.com/click/altium?sku=2435499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)
34 | C905 | 1 | 22u/50V | MLCC | 2220 | KEMET (https://octopart-clicks.com/click/altium?sku=399-5797-1-ND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) | C2220C226M5R2CAUTO (https://octopart-clicks.com/click/altium?sku=399-5797-1-ND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) | Digi-Key | 399-5797-1-ND (https://octopart-clicks.com/click/altium?sku=399-5797-1-ND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)
35 | D1100 | 1 | BAT54C,215 | Schottky Barrier Diode, 30 V, 3-Pin SOT23, RoHS, Tape and Reel |  | NXP Semiconductors | BAT54C,215
36 | D1401-1, D1401-2 | 2 | SMAJ60A-E3/61 | Transient Voltage Suppressor, 6.40 to 231 V, 60 V Stand-off Voltage, Uni-Directional, -55 to 155 degC, 2-pin DO-214AC, Pb-Free, Tape and Reel |  | Vishay Semiconductors (https://octopart-clicks.com/click/altium?sku=1837055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) | SMAJ60A-E3/61 (https://octopart-clicks.com/click/altium?sku=1837055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) | Farnell | 1837055 (https://octopart-clicks.com/click/altium?sku=1837055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)
37 | D900 | 1 | PDS3200 | Schottky Diode 3A 200V 780mV |  | Diodes (https://octopart-clicks.com/click/altium?sku=1713904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) | PDS3200-13 (https://octopart-clicks.com/click/altium?sku=1713904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) | Farnell | 1713904 (https://octopart-clicks.com/click/altium?sku=1713904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)
38 | D901, D1400-1, D1400-2 | 3 | DFLS1100-7 | 1 A High Voltage Schottky Barrier Rectifier, 0.62 V, -55 to 175 degC, 2- Pin POWERDI123, Pb-Free, Tape and Reel |  | Diodes (https://octopart-clicks.com/click/altium?sku=1713889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) | DFLS1100-7 (https://octopart-clicks.com/click/altium?sku=1713889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) | Farnell | 1713889 (https://octopart-clicks.com/click/altium?sku=1713889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)
39 | Z1300-1, Z1300-2, Z1301-1, Z1301-2, Z1302-1, Z1302-2, Z1303-1, Z1303-2, Z1304-1, Z1304-2, Z1305-1, Z1305-2, Z1306-1, Z1306-2, Z1307-1, Z1307-2, Z1308-1, Z1308-2, Z1309-1, Z1309-2, Z1310-1, Z1310-2, Z1311-1, Z1311-2 | 24 | MMSZ4692T1G | Zener Voltage Regulator, 500 mW, 2-Pin SOD-123, Pb-Free, Tape and Reel |  | ON Semiconductor (https://octopart-clicks.com/click/altium?sku=MMSZ4692T1GOSCT-ND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) | MMSZ4692T1G (https://octopart-clicks.com/click/altium?sku=MMSZ4692T1GOSCT-ND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) | Digi-Key | MMSZ4692T1GOSCT-ND (https://octopart-clicks.com/click/altium?sku=MMSZ4692T1GOSCT-ND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)
40 | LD1400-1, LD1400-2 | 2 | green | LED |  | Kingbright (https://octopart-clicks.com/click/altium?sku=2099223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) | KPT-1608SGC (https://octopart-clicks.com/click/altium?sku=2099223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) | Farnell | 2099223 (https://octopart-clicks.com/click/altium?sku=2099223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)
41 | F300, F314 | 2 | fuse_0.5A_0448.500MR | Fuse, Surface Mount, NANO2 Series, 500 mA, 125 VAC, 32 VDC, Very Fast Acting, SMD |  | Littelfuse (https://octopart-clicks.com/click/altium?sku=1596919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) | 0448.500MR (https://octopart-clicks.com/click/altium?sku=1596919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) | Farnell | 1596919 (https://octopart-clicks.com/click/altium?sku=1596919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)
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

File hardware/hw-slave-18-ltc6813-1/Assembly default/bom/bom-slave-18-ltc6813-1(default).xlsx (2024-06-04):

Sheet: BOM
BOM for slave-18-ltc6813-1, Variant default
Generated on 14.12.2018 14:27:44
Line # | Designator | Quantity | Name | Description | Case EIA | Manufacturer 1 | Manufacturer Part Number 1 | Supplier 1 | Supplier Part Number 1 | Automotive Qualified
1 | R610_1, R610_2, R1407_1, R1407_2, R1409_1, R1409_2, R1411_1, R1411_2, R1413_1, R1413_2, R1415_1, R1415_2, R1417_1, R1417_2 | 14 | 0R | SMD Resistor 0R 0603 | 0603 | Vishay Semiconductors (https://octopart-clicks.com/click/altium?sku=2616580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) | RCA06030000ZSEA (https://octopart-clicks.com/click/altium?sku=2616580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) | Farnell | 2616580 (https://octopart-clicks.com/click/altium?sku=2616580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) | True
2 | R108_1, R108_2, R109_1, R109_2, R112_1, R112_2, R113_1, R113_2, R114_1, R114_2, R115_1, R115_2, R116_1, R116_2, R117_1, R117_2, R118_1, R118_2, R119_1, R119_2, R1300_1, R1300_2, R1301_1, R1301_2, R1302_1, R1302_2, R1303_1, R1303_2, R1304_1, R1304_2, R1305_1, R1305_2, R1306_1, R1306_2, R1307_1, R1307_2, R1308_1, R1308_2, R1309_1, R1309_2, R1310_1, R1310_2, R1311_1, R1311_2, R1312_1, R1312_2, R1313_1, R1313_2, R1314_1, R1314_2, R1315_1, R1315_2, R1316_1, R1316_2, R1317_1, R1317_2, R1318_1, R1318_2 | 58 | 100R | SMD Resistor 100R 0603 | 0603 | Panasonic (https://octopart-clicks.com/click/altium?sku=P100HCT-ND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) | ERJ-3EKF1000V (https://octopart-clicks.com/click/altium?sku=P100HCT-ND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) | Digi-Key | P100HCT-ND (https://octopart-clicks.com/click/altium?sku=P100HCT-ND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) | True
3 | R1405_1, R1405_2, R1418_1, R1418_2 | 4 | 120R | SMD Resistor 120R 0603 | 0603 | Vishay (https://octopart-clicks.com/click/altium?sku=1652832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) | CRCW0603120RFKEA (https://octopart-clicks.com/click/altium?sku=1652832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) | Farnell | 1652832 (https://octopart-clicks.com/click/altium?sku=1652832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) | True
4 | R1100, R1101, R1102, R1103, R1104, R1105, R1106, R1107, R1108, R1109, R1110, R1111, R1112, R1113, R1114, R1115, R1116, R1117 | 18 | 150R | SMD Resistor 150R 0603 | 0603 | Panasonic (https://octopart-clicks.com/click/altium?sku=2303076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) | ERJ-3EKF1500V (https://octopart-clicks.com/click/altium?sku=2303076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) | Farnell | 2303076 (https://octopart-clicks.com/click/altium?sku=2303076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) | True
5 | R1403_1, R1403_2 | 2 | 270R | SMD Resistor 270R 0603 | 0603 | Vishay (https://octopart-clicks.com/click/altium?sku=2141320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) | CRCW0603270RFKEA (https://octopart-clicks.com/click/altium?sku=2141320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) | Farnell | 2141320 (https://octopart-clicks.com/click/altium?sku=2141320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) | True
6 | R1402_1, R1402_2 | 2 | 820R | SMD Resistor 820R 0603 | 0603 | Vishay (https://octopart-clicks.com/click/altium?sku=1469841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) | CRCW0603820RFKEA (https://octopart-clicks.com/click/altium?sku=1469841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) | Farnell | 1469841 (https://octopart-clicks.com/click/altium?sku=1469841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) | True
7 | R603_1, R603_2 | 2 | 1k | SMD Resistor 1k 0603 | 0603 | Vishay Dale (https://octopart-clicks.com/click/altium?sku=1652848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) | CRCW06031K00FKTA (https://octopart-clicks.com/click/altium?sku=1652848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) | Farnell | 1652848 (https://octopart-clicks.com/click/altium?sku=1652848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) | True
8 | R1400_1, R1400_2, R1419_1, R1419_2, R1420_1, R1420_2 | 6 | 1k2 | SMD Resistor 1k2 0603 | 0603 | Multicomp (https://octopart-clicks.com/click/altium?sku=2073370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) | MCMR06X1201FTL (https://octopart-clicks.com/click/altium?sku=2073370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) | Farnell | 2073370 (https://octopart-clicks.com/click/altium?sku=2073370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) | True
9 | R602_1, R602_2 | 2 | 1k5 | SMD Resistor 1k5 0603 | 0603 | Vishay Dale (https://octopart-clicks.com/click/altium?sku=2616745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) | CRCW06031K50JNEA (https://octopart-clicks.com/click/altium?sku=2616745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) | Farnell | 2616745 (https://octopart-clicks.com/click/altium?sku=2616745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) | True
10 | R600_1, R600_2, R606_1, R606_2 | 4 | 124k | SMD Resistor 124k 0603 | 0603 | Vishay (https://octopart-clicks.com/click/altium?sku=2138508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) | CRCW0603124KFKEA (https://octopart-clicks.com/click/altium?sku=2138508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) | Farnell | 2138508 (https://octopart-clicks.com/click/altium?sku=2138508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) | True
11 | R1512, R1513, R1514, R1515, R1516, R1517, R1530, R1531, R1532, R1533, R1534, R1535, R1548, R1549, R1550, R1551, R1552, R1553 | 18 | 3k3 | SMD Resistor 3k3 0603 | 0603 | Panasonic (https://octopart-clicks.com/click/altium?sku=2303173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) | ERJ-3EKF3301V (https://octopart-clicks.com/click/altium?sku=2303173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) | Farnell | 2303173 (https://octopart-clicks.com/click/altium?sku=2303173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) | True
12 | R100_1, R100_2, R101_1, R101_2, R102_1, R102_2, R103_1, R103_2, R104_1, R104_2, R105_1, R105_2, R106_1, R106_2, R107_1, R107_2, R601_1, R601_2, R605_1, R605_2, R607_1, R607_2, R700_1, R700_2, R701_1, R701_2, R702_1, R702_2, R703_1, R703_2, R704_1, R704_2, R705_1, R705_2, R706_1, R706_2, R707_1, R707_2, R708_1, R708_2, R800_1, R800_2, R905, R1118, R1421_1, R1421_2, R1422_1, R1422_2, R1423_1, R1423_2, R1424_1, R1424_2 | 52 | 10k | SMD Resistor 10k 0603 | 0603 | Multicomp (https://octopart-clicks.com/click/altium?sku=2073349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) | MCMR06X1002FTL (https://octopart-clicks.com/click/altium?sku=2073349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) | Farnell | 2073349 (https://octopart-clicks.com/click/altium?sku=2073349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) | True
13 | R901 | 1 | 86k6 | SMD Resistor 86k6 0603 | 0603 | Panasonic (https://octopart-clicks.com/click/altium?sku=2059490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) | ERJ-3EKF8662V (https://octopart-clicks.com/click/altium?sku=2059490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) | Farnell | 2059490 (https://octopart-clicks.com/click/altium?sku=2059490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) | True
14 | R608_1, R608_2 | 2 | 68k | SMD Resistor 68k 0603 | 0603 |  |  |  |  | False
15 | R904 | 1 | 220k | SMD Resistor 220k 0603 | 0603 |  |  |  |  | False
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

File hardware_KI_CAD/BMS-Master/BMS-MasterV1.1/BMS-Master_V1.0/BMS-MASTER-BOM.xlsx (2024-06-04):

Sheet: ListeMatériels_PV_Master
Fournisseur | Nbr. | N° article | Référence | Valeur | Empreinte | Description | Fitted (X) | Generic (X) | Through-hole (X) | prix unitaire | prix total
BOM BMS-Master |  |  |  |  |  |  |  |  |  | Liste actualisée le : 22.01.2024
Composants électriques et électroniques
 | 6 | generic | C1, C2, C7, C8, C32, C33 | 18pF/50V | 0603_1608Metric | capa 18pF/50V | x | x |  |  | 0.00 CHF
 | 44 | generic | C3, C4, C9-C25, C27-C31, C34-C40, C42, C70, C77, C85-C90, C105, C106, C108, C111 | 100nF/50V | 0603_1608Metric | capa 100nF/50V | x | x |  |  | 0.00 CHF
 | 4 | generic | C5, C6, C41, C43 | 2u2/10V | 0603_1608Metric | capa 2u2/10V | x | x |  |  | 0.00 CHF
 | 4 | generic | C26, C91, C92, C107 | 1uF/35V | 0603_1608Metric | capa 1uF/35V | x | x |  |  | 0.00 CHF
 | 32 | generic | C44, C46, C47, C49-C53, C56-C59, C62-C67, C76, C80-C84, C93-C100 | 100n/50V | 0603_1608Metric | capa 100nF/50V | x | x |  |  | 0.00 CHF
 | 2 | generic | C45, C48 | 4u7/25V | 0603_1608Metric | capa 4u7/25V | x | x |  |  | 0.00 CHF
 | 4 | generic | C54, C55, C60, C61 | 27pF/50V | 0603_1608Metric | capa 27pF/50V | x | x |  |  | 0.00 CHF
 | 4 | generic | C68, C72, C73, C78 | 10u/50V | 0805_2012Metric | capa10uF/50V | x | x |  |  | 0.00 CHF
 | 4 | generic | C69, C74, C75, C79 | 0.1u/50V | 0603_1608Metric | capa 0.1uF/50V | x | x |  |  | 0.00 CHF
 | 1 | generic | C71 | 68uF/50V | 0805_2012Metric | capa 68uF/50V | x | x |  |  | 0.00 CHF
 | 2 | generic | C101, C102 | 10uF/50V | 1206_3216Metric | capa 10uF/50V | x | x |  |  | 0.00 CHF
 | 1 | generic | C103 | 10uF/50V | 1210_3225Metric | capa 10uF/50V | x | x |  |  | 0.00 CHF
Mouser | 1 | 581-AEA0810560M050R | C104 | 56uF/50V | CP_Elec_8x10 | Aluminium Electrolytic Capacitors - SMD 50V 56pF 0810 20% | x |  |  | 0.66 | 0.66 CHF
 | 2 | generic | C109, C110 | 47uF/25V | C_1206_3216Metric | capa 47uF/25V | x | x |  |  | 0.00 CHF
Mouser | 2 | 78-TLMS1100-GS15 | D1, D3 | LED_RED | LED_0603_1608Metric | Standard LEDs - SMD CHIPLED(SMD 0603-LED) RED-E4 | x |  |  | 0.40 | 0.80 CHF
Mouser | 2 | 78-TLMG1100-GS15 | D2, D4 | LED_Green | LED_0603_1608Metric | Standard LEDs - SMD CHIPLED(SMD 0603-LED) GREEN U.BRIGHT-E4 | x |  |  | 0.40 | 0.80 CHF
Mouser | 3 | 625-GF1B-E3 | D5, D6, D10 | GF1B-E3_67A | GF1 (DO-214BA) | Rectifiers 1.0 Amp 100 Volt | x |  |  | 0.40 | 1.20 CHF
Mouser | 3 | 652-CDSOD323-T05 | D7-D9 | CDSOD323-T05 | SOD-323 | ESD Suppressors / TVS Diodes TVS Diode 5VOLT | x |  |  | 0.53 | 1.59 CHF
Mouser | 2 | 78-TLMO1100-GS15 | D11, D13 | LED orange | LED_0603_1608Metric | Standard LEDs - SMD CHIPLED(SMD 0603-LED) S.ORANGE ULTRA-E4 | x |  |  | 0.40 | 0.80 CHF
Mouser | 1 | 771-BZV55-B15-T/R | D12 | BZV55B15 | MiniMELF | Zener Diodes BZV55-B15/SOD80/LLDS | x |  |  | 0.21 | 0.21 CHF
Mouser | 1 | 576-0408002.WR | F1 | 0408002.WR | Fuse_0603_1608Metric | Surface Mount Fuses FUSE 32V HIGH I2T 0603 TL 2A | x |  |  | 1.17 | 1.17 CHF
Mouser | 1 | 530-0ABB-7000-TM | F2 | 0408007.WR | Fuse_0603_1608Metric | Surface Mount Fuses 0603 SMD Fuse. Slow Blow 7A | x |  |  | 0.70 | 0.70 CHF
Mouser | 1 | 595-SN74LVC08AD | IC1 | SN74LVC08AD | SOIC-14 | Logic Gates Quad 2-Input AND | x |  |  | 0.86 | 0.86 CHF
Mouser | 2 | 595-SN74LVC1G332DBVR | IC2, IC6 | SN74LVC1G332DBVR | SOT-23-6 | Logic Gates Sngl 3 Inpt + OR Gt | x |  |  | 0.36 | 0.72 CHF
Mouser | 2 | 576-LS1205EFD33 | IC3, IC7 | LS1205EF | DFN3x3_10 | Power Switch ICs - Power Distribution 18V/5A efuse with OCP & Fault Indication | x |  |  | 1.30 | 2.60 CHF
Mouser | 1 | 595-SN74HC04DRG3 | IC4 | SN74HC04DR | SOIC-14 | Inverters Hex Inverters 6 gates | x |  |  | 0.48 | 0.48 CHF
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

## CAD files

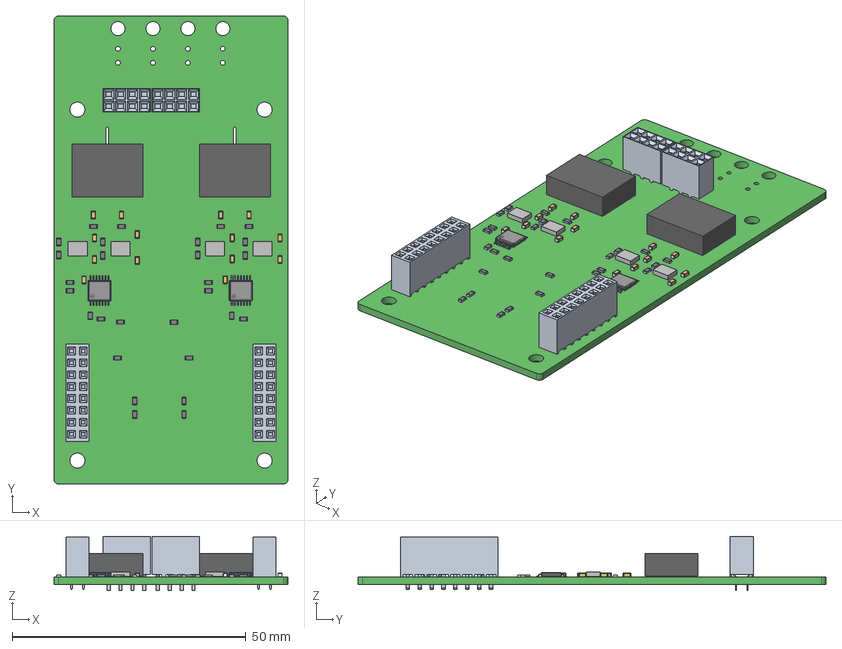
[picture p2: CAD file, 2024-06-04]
hardware/hw-interface-ltc6820/Assembly default/Export STEP/interface(default).step
50.0 x 100.0 x 11.6 mm
Board
Mid_Body x 28
Open_CASCADE_STEP_translator_6.8_9.2.1 x 56
Mark x 28
c-534206-4-n-3d x 2
Extruded x 6
BODY_MTC14 x 2
LEAD_MTC14 x 28
Open_CASCADE_STEP_translator_6.8_2.1.1 x 14
Open_CASCADE_STEP_translator_6.8_2.1.2 x 14
Open_CASCADE_STEP_translator_6.8_2.2.1 x 14
SSW-108-01-X-D x 2

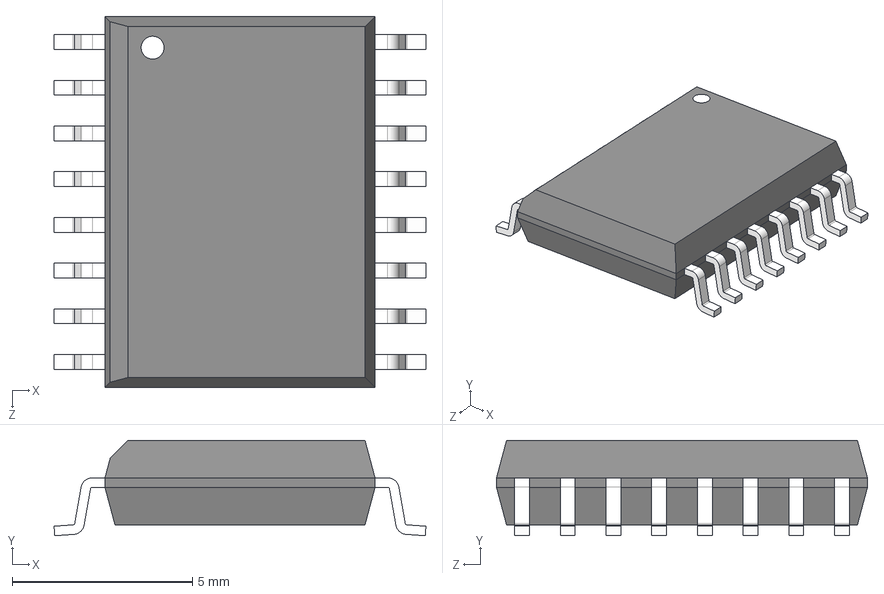
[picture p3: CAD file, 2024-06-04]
hardware_KI_CAD/components/master/ADUM3300CRWZ/ADUM3300CRWZ.step
10.3 x 2.65 x 10.3 mm

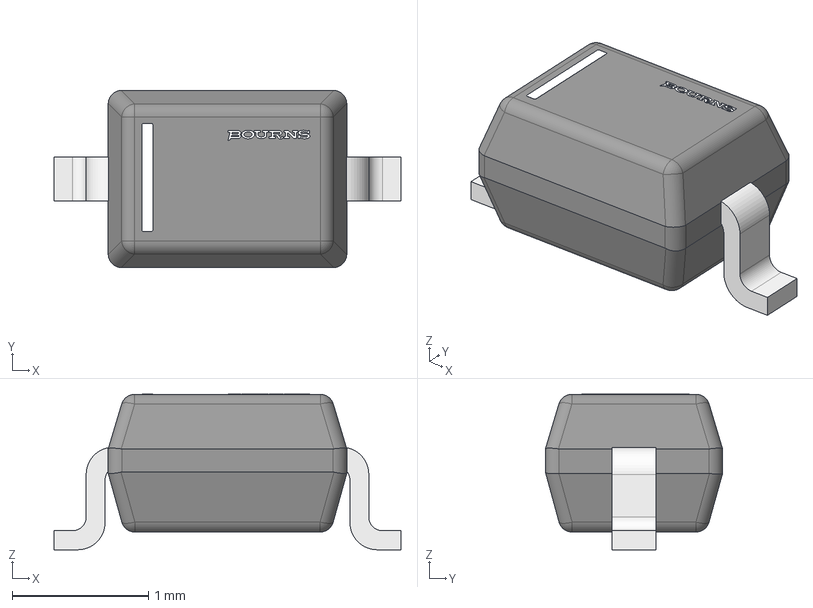
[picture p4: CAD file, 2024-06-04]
hardware_KI_CAD/components/master/CDSOD323-T05/Bourns_Inc._-_CDSOD323-T05.step
2.54 x 1.30 x 1.14 mm

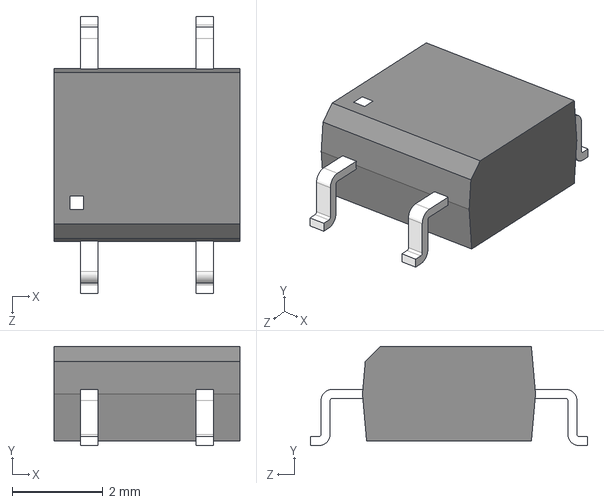
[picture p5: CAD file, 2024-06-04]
hardware_KI_CAD/components/master/CPC1008N/CPC1008N.step
4.09 x 2.18 x 6.10 mm

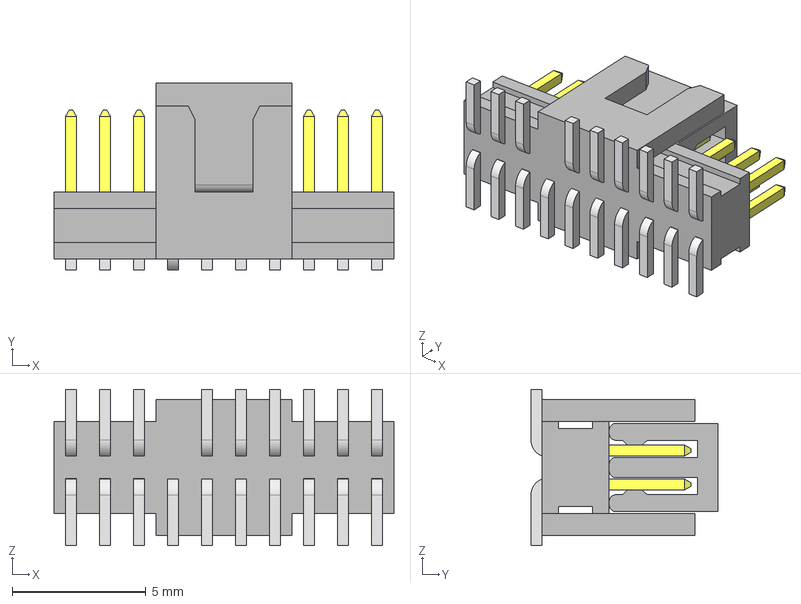
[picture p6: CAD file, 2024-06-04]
hardware_KI_CAD/components/master/FTSH-110-01-L-DV-007-K-P/FTSH-110-01-L-DV-007.step
12.7 x 6.98 x 5.84 mm
FTSH-110-01-L-DV-007-K-P_pp_pad
FTSH-110-01-L-DV-007-K-P_pins2
FTSH-110-01-L-DV-007-K-P_pins1
FTSH-110-01-L-DV-007-K-P_body

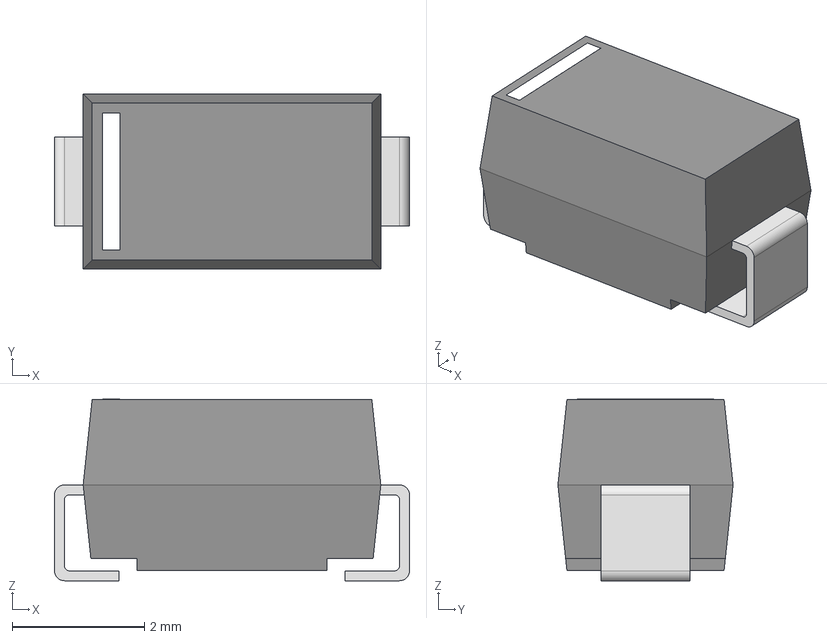
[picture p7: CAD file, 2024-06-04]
hardware_KI_CAD/components/master/GF1B-E367A/GF1B-E367A.step
5.36 x 2.65 x 2.74 mm
pins
marking

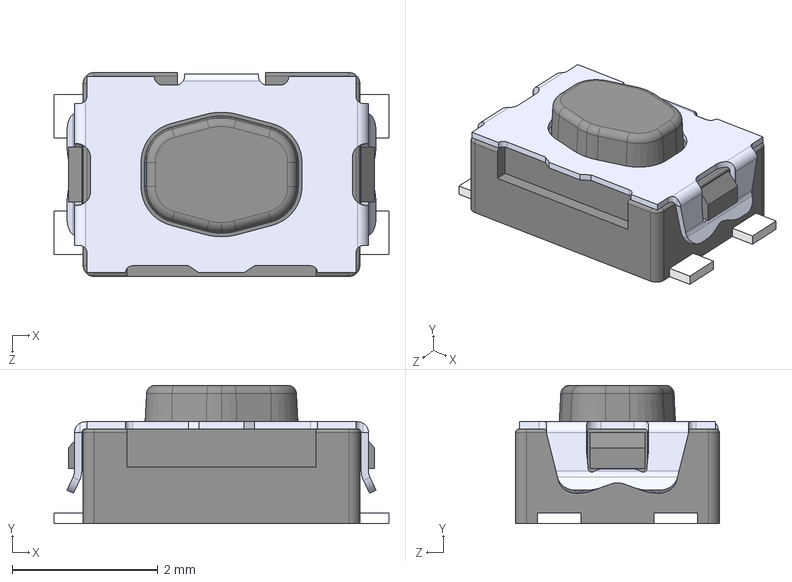
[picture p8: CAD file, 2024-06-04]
hardware_KI_CAD/components/master/KMR221GLFS/KMR221GLFS.step
4.60 x 1.90 x 2.80 mm

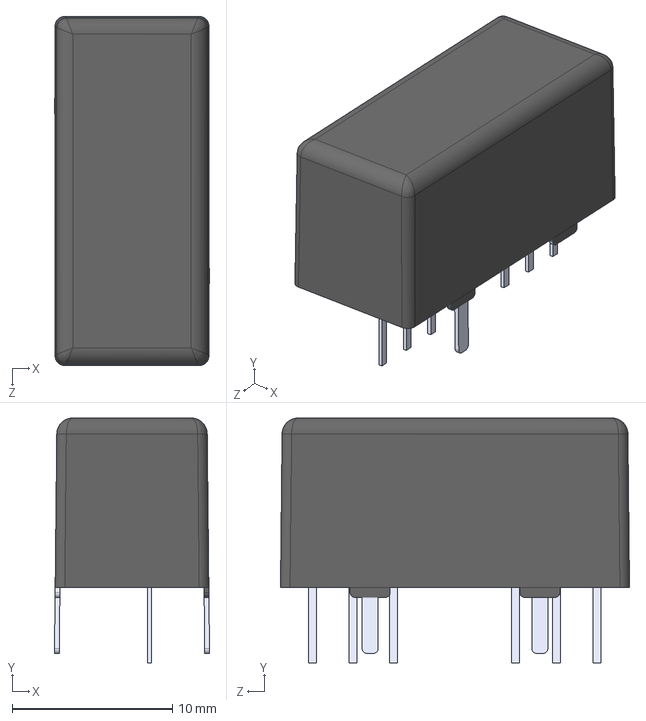
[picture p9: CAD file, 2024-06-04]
hardware_KI_CAD/components/master/TMR 9-1211/TMR_9-1211.step
9.69 x 15.3 x 21.8 mm

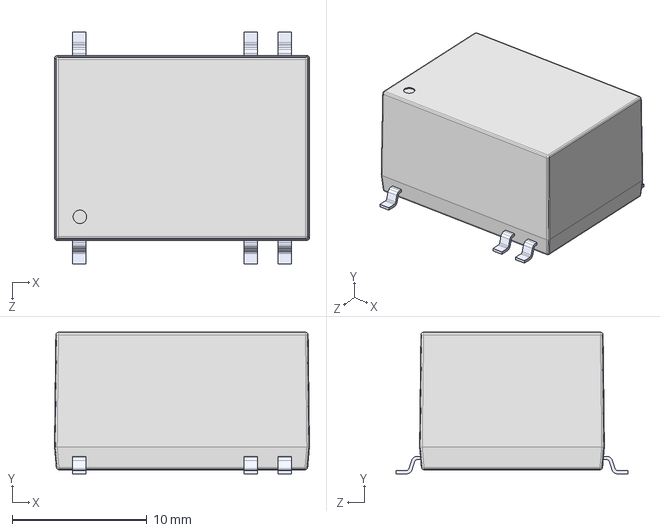
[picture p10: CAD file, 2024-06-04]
hardware_KI_CAD/components/master/TRI 1-1211SM/TRI_1-1211SM.step
18.9 x 10.5 x 17.2 mm

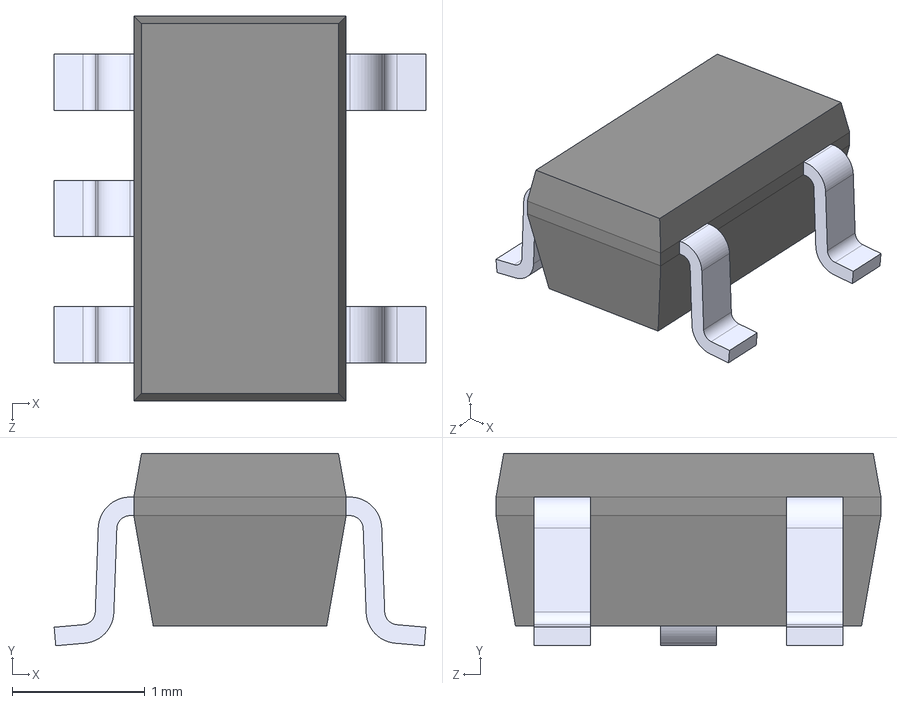
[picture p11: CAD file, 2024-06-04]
hardware_KI_CAD/components/master_pcb/AD8628ARTZ-R2/AD8628ARTZ-R2.step
2.80 x 1.45 x 2.90 mm

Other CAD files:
hardware_KI_CAD/components/Slave/43045-0412/43045-0412--3DModel-STEP-56544.STEP
hardware_KI_CAD/components/Slave/LTC6811HG-1#PBF/LTC6811HG-1_PBF.step
hardware_KI_CAD/components/master/43045-0412/43045-0412--3DModel-STEP-56544.STEP
hardware_KI_CAD/components/master_pcb/43045-0412/43045-0412--3DModel-STEP-56544.STEP
hardware_KI_CAD/components/pcb_components/430450225/43045-0225.step
hardware_KI_CAD/components/pcb_components/430452425/430452425.step
hardware_KI_CAD/components/pcb_components/PBSS4112PANP,115/PBSS4112PANP_115.step

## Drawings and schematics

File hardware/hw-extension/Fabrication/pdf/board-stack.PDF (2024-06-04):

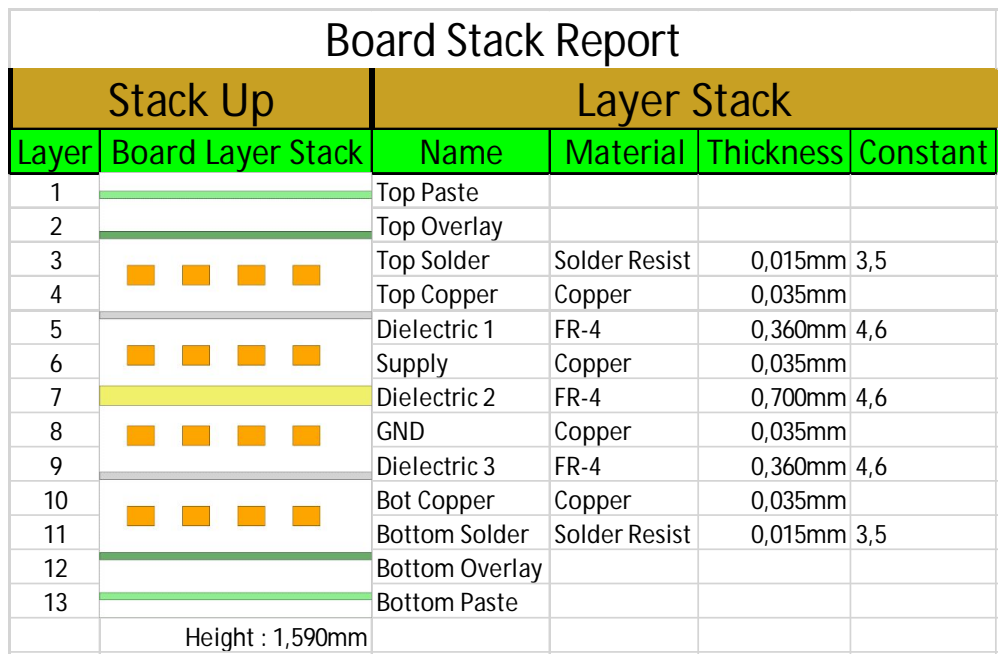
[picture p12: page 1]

Stack Up | Layer Stack
Layer | Board Layer Stack | Name | Material | Thickness | Constant
1 | | Top Paste
2 | | Top Overlay
3 | | Top Solder | Solder Resist | 0,015mm | 3,5
4 | | Top Copper | Copper | 0,035mm
5 | | Dielectric 1 | FR-4 | 0,360mm | 4,6
6 | | Supply | Copper | 0,035mm
7 | | Dielectric 2 | FR-4 | 0,700mm | 4,6
8 | | GND | Copper | 0,035mm
9 | | Dielectric 3 | FR-4 | 0,360mm | 4,6
10 | | Bot Copper | Copper | 0,035mm
11 | | Bottom Solder | Solder Resist | 0,015mm | 3,5
12 | | Bottom Overlay
13 | | Bottom Paste

Height : 1,590mm

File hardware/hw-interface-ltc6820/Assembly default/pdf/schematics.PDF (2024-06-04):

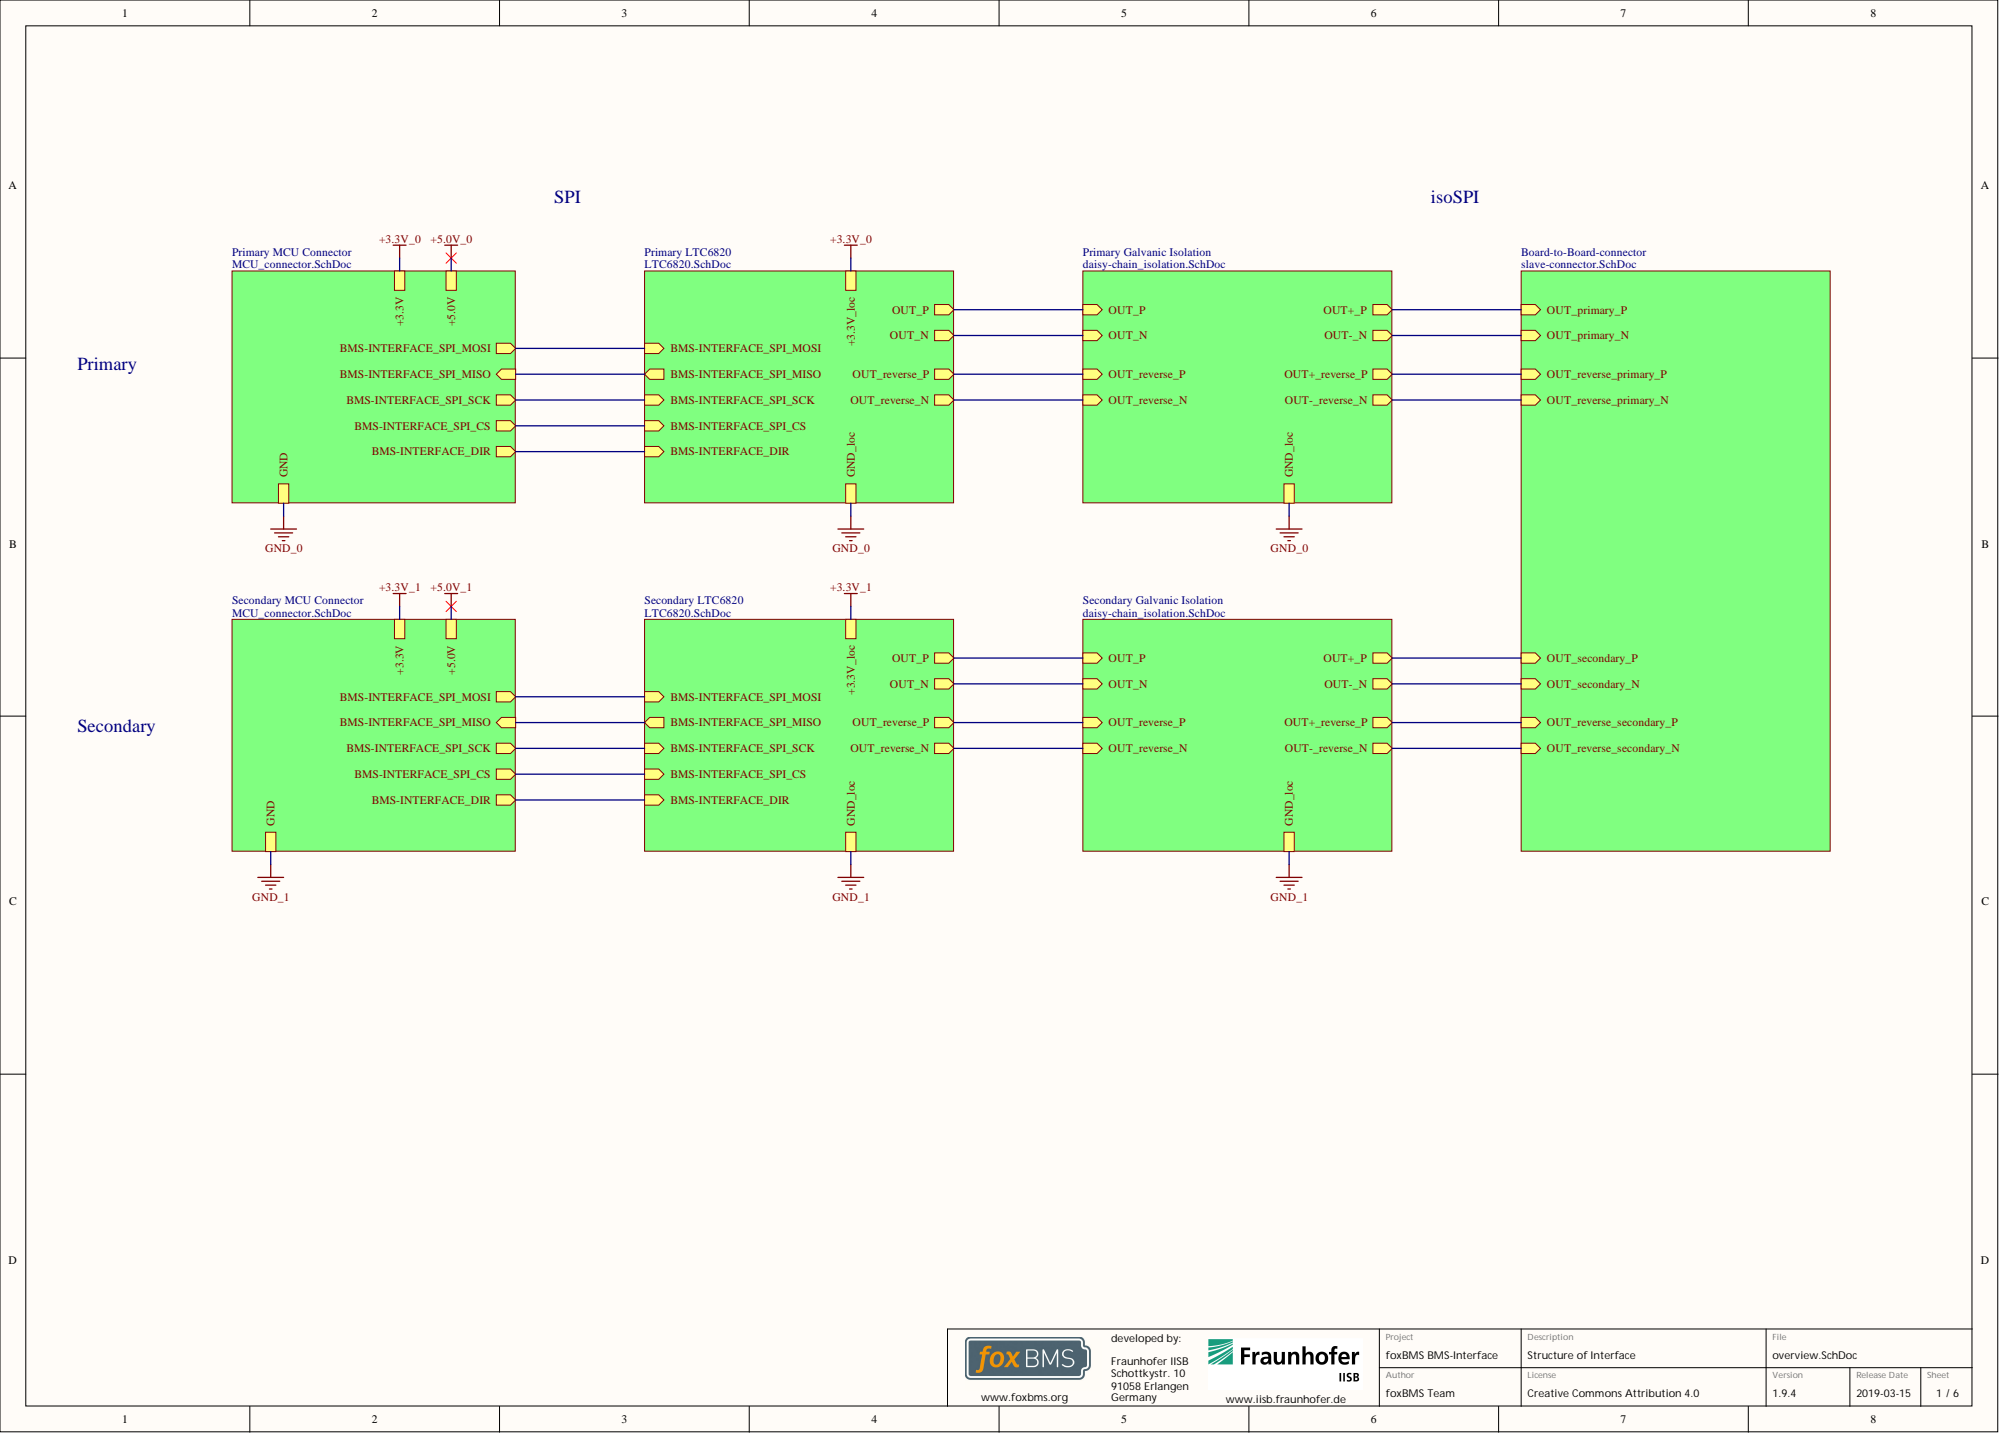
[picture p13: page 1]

Board-to-Board-connector
slave-connector.SchDoc

www.iisb.fraunhofer.de

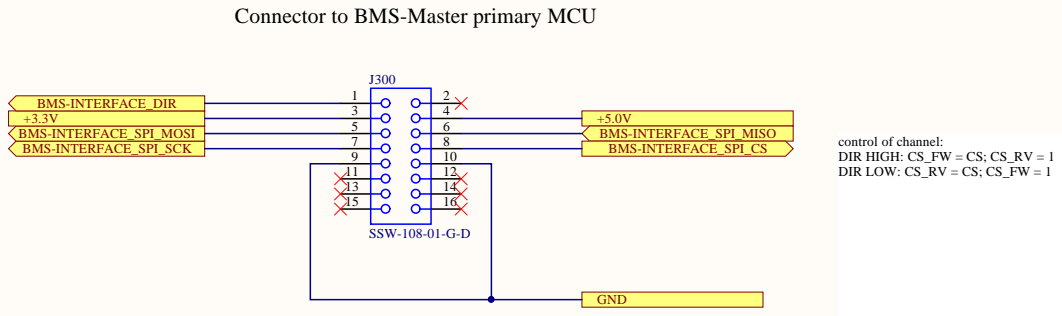
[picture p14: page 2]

Connector to BMS-Master primary MCU

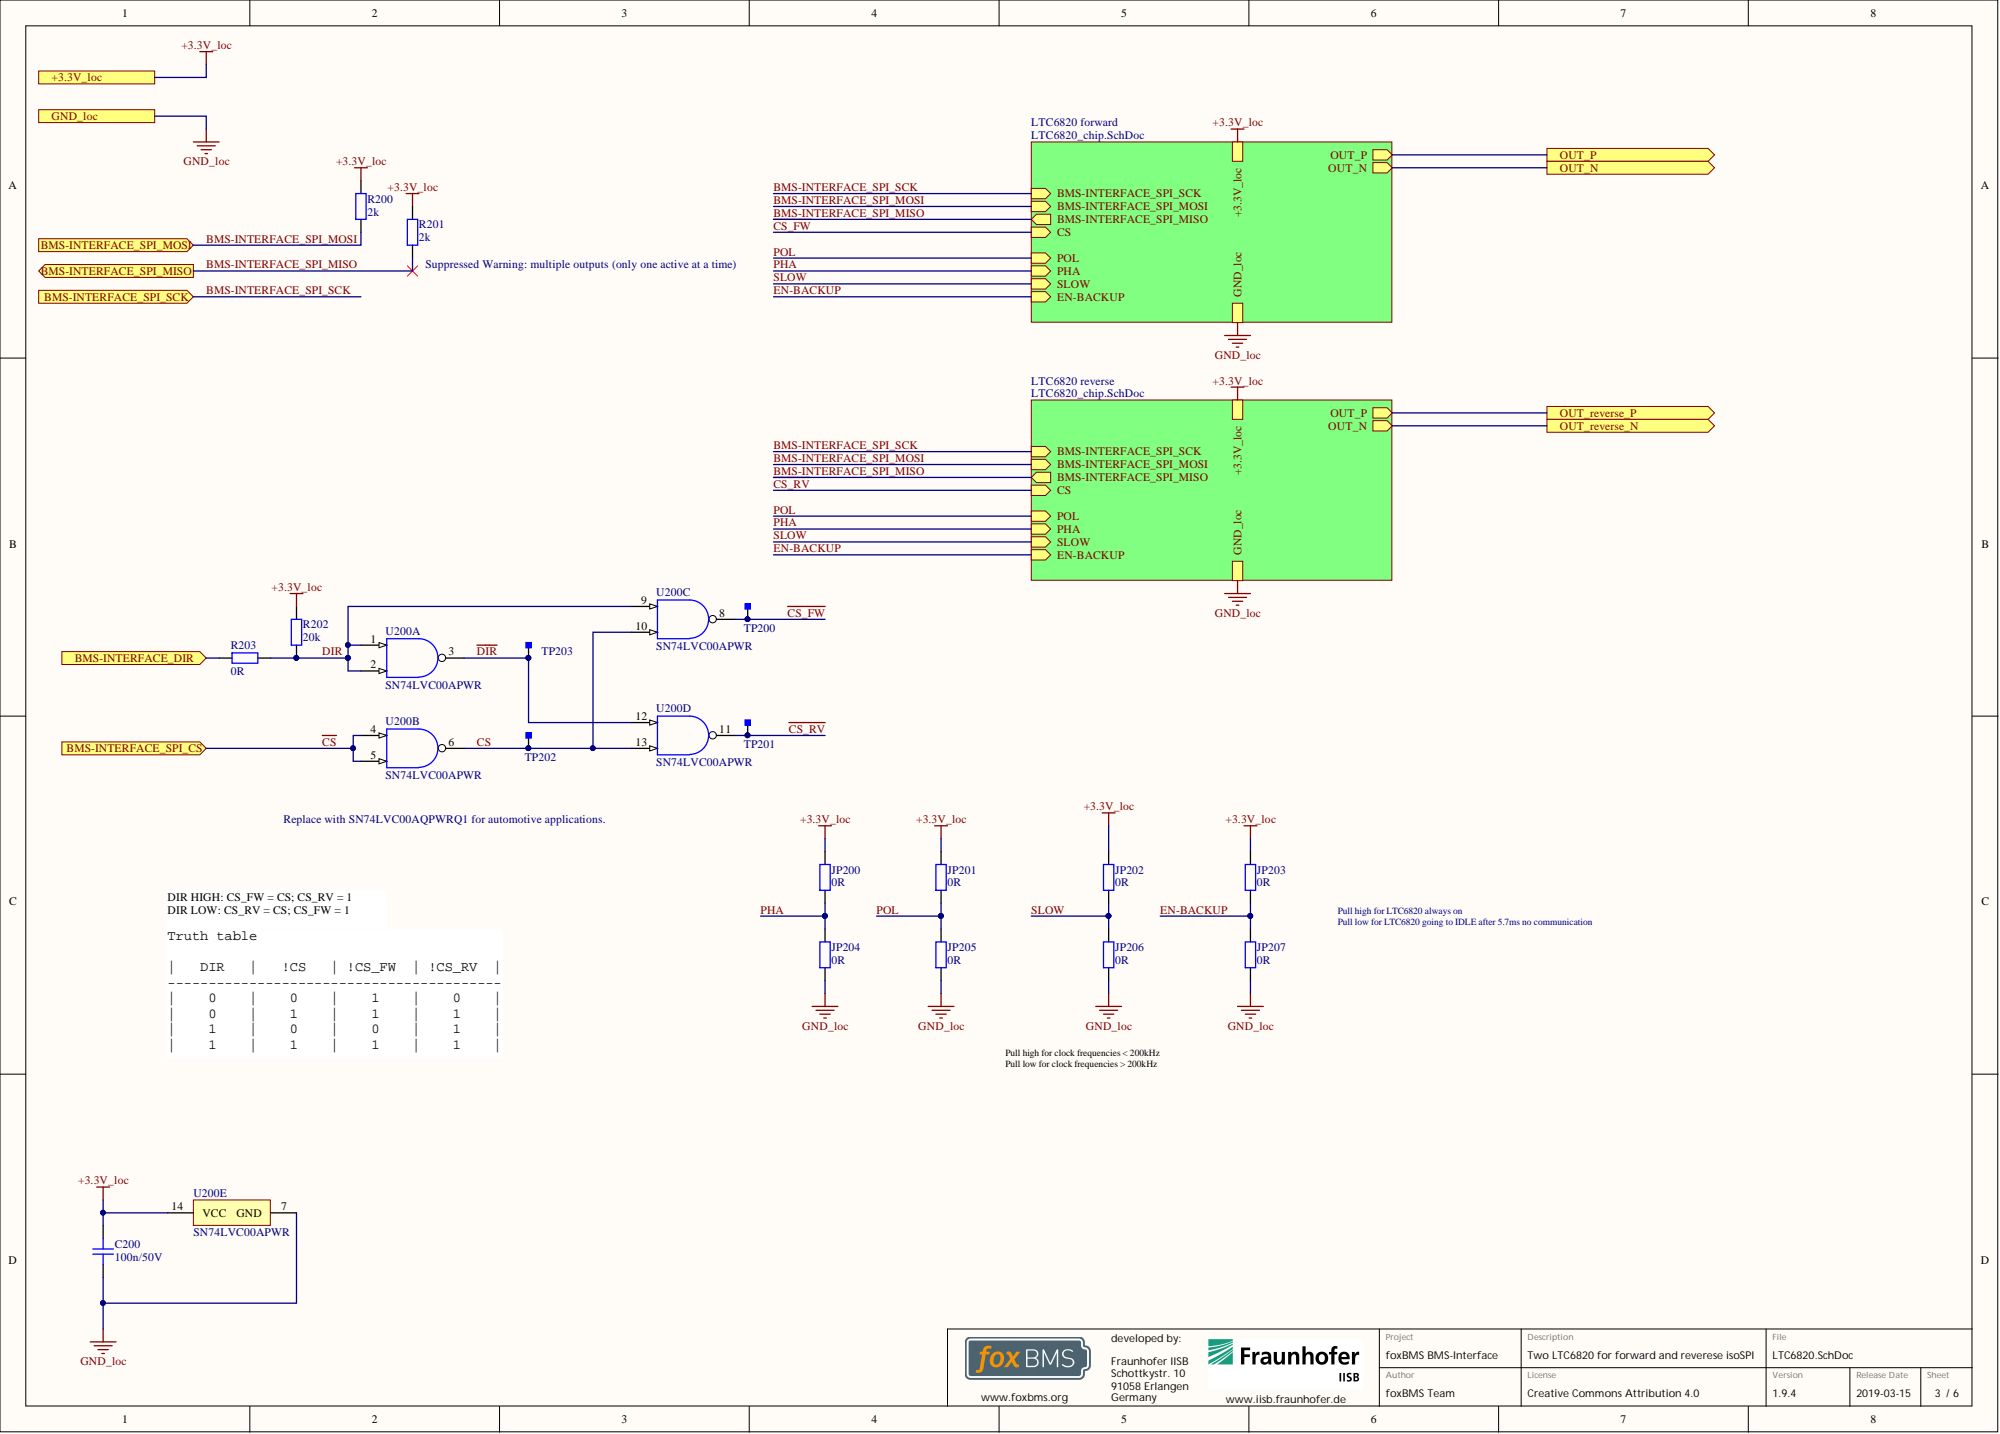
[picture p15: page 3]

Suppressed Warning: multiple outputs (only one active at a time)

Replace with SN74LVC00AQPWRQ1 for automotive applications.

Pull high for LTC6820 always on
Pull low for LTC6820 going to IDLE after 5.7ms no communication

Pull high for clock frequencies < 200kHz
Pull low for clock frequencies > 200kHz

Two LTC6820 for forward and reverese isoSPI

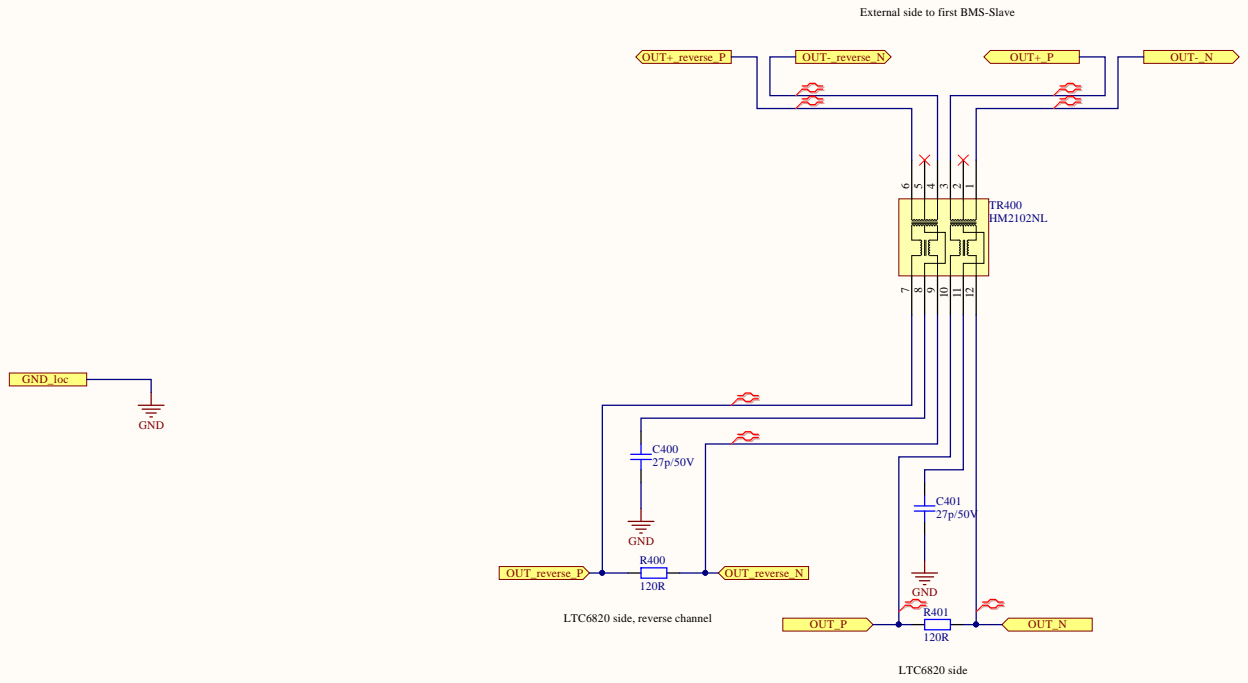
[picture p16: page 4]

External side to first BMS-Slave

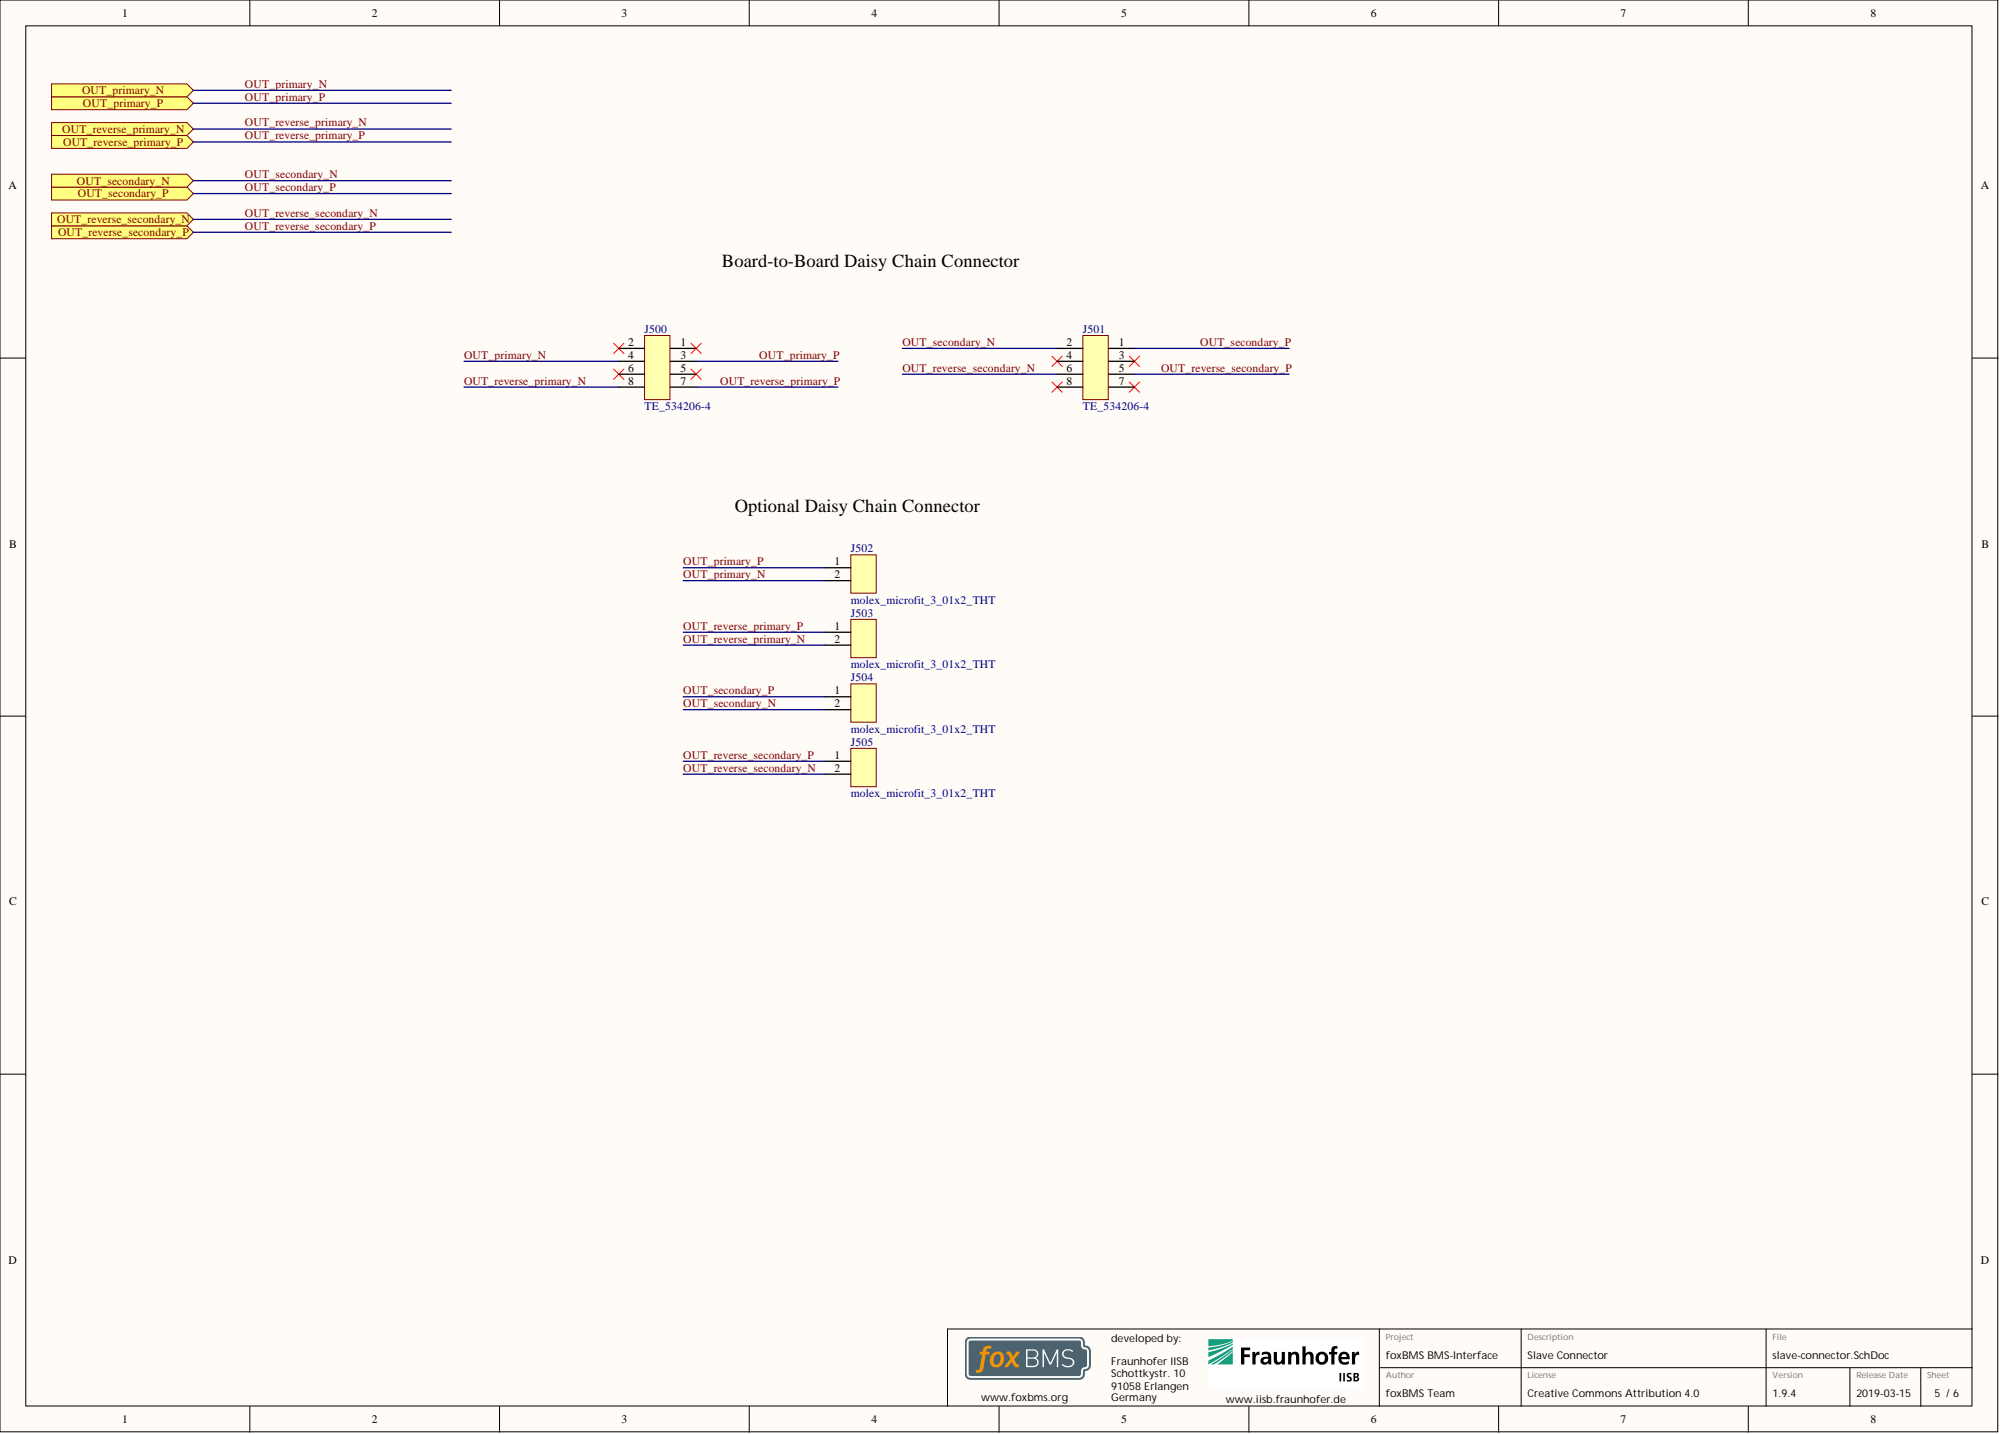
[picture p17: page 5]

Board-to-Board Daisy Chain Connector

Optional Daisy Chain Connector

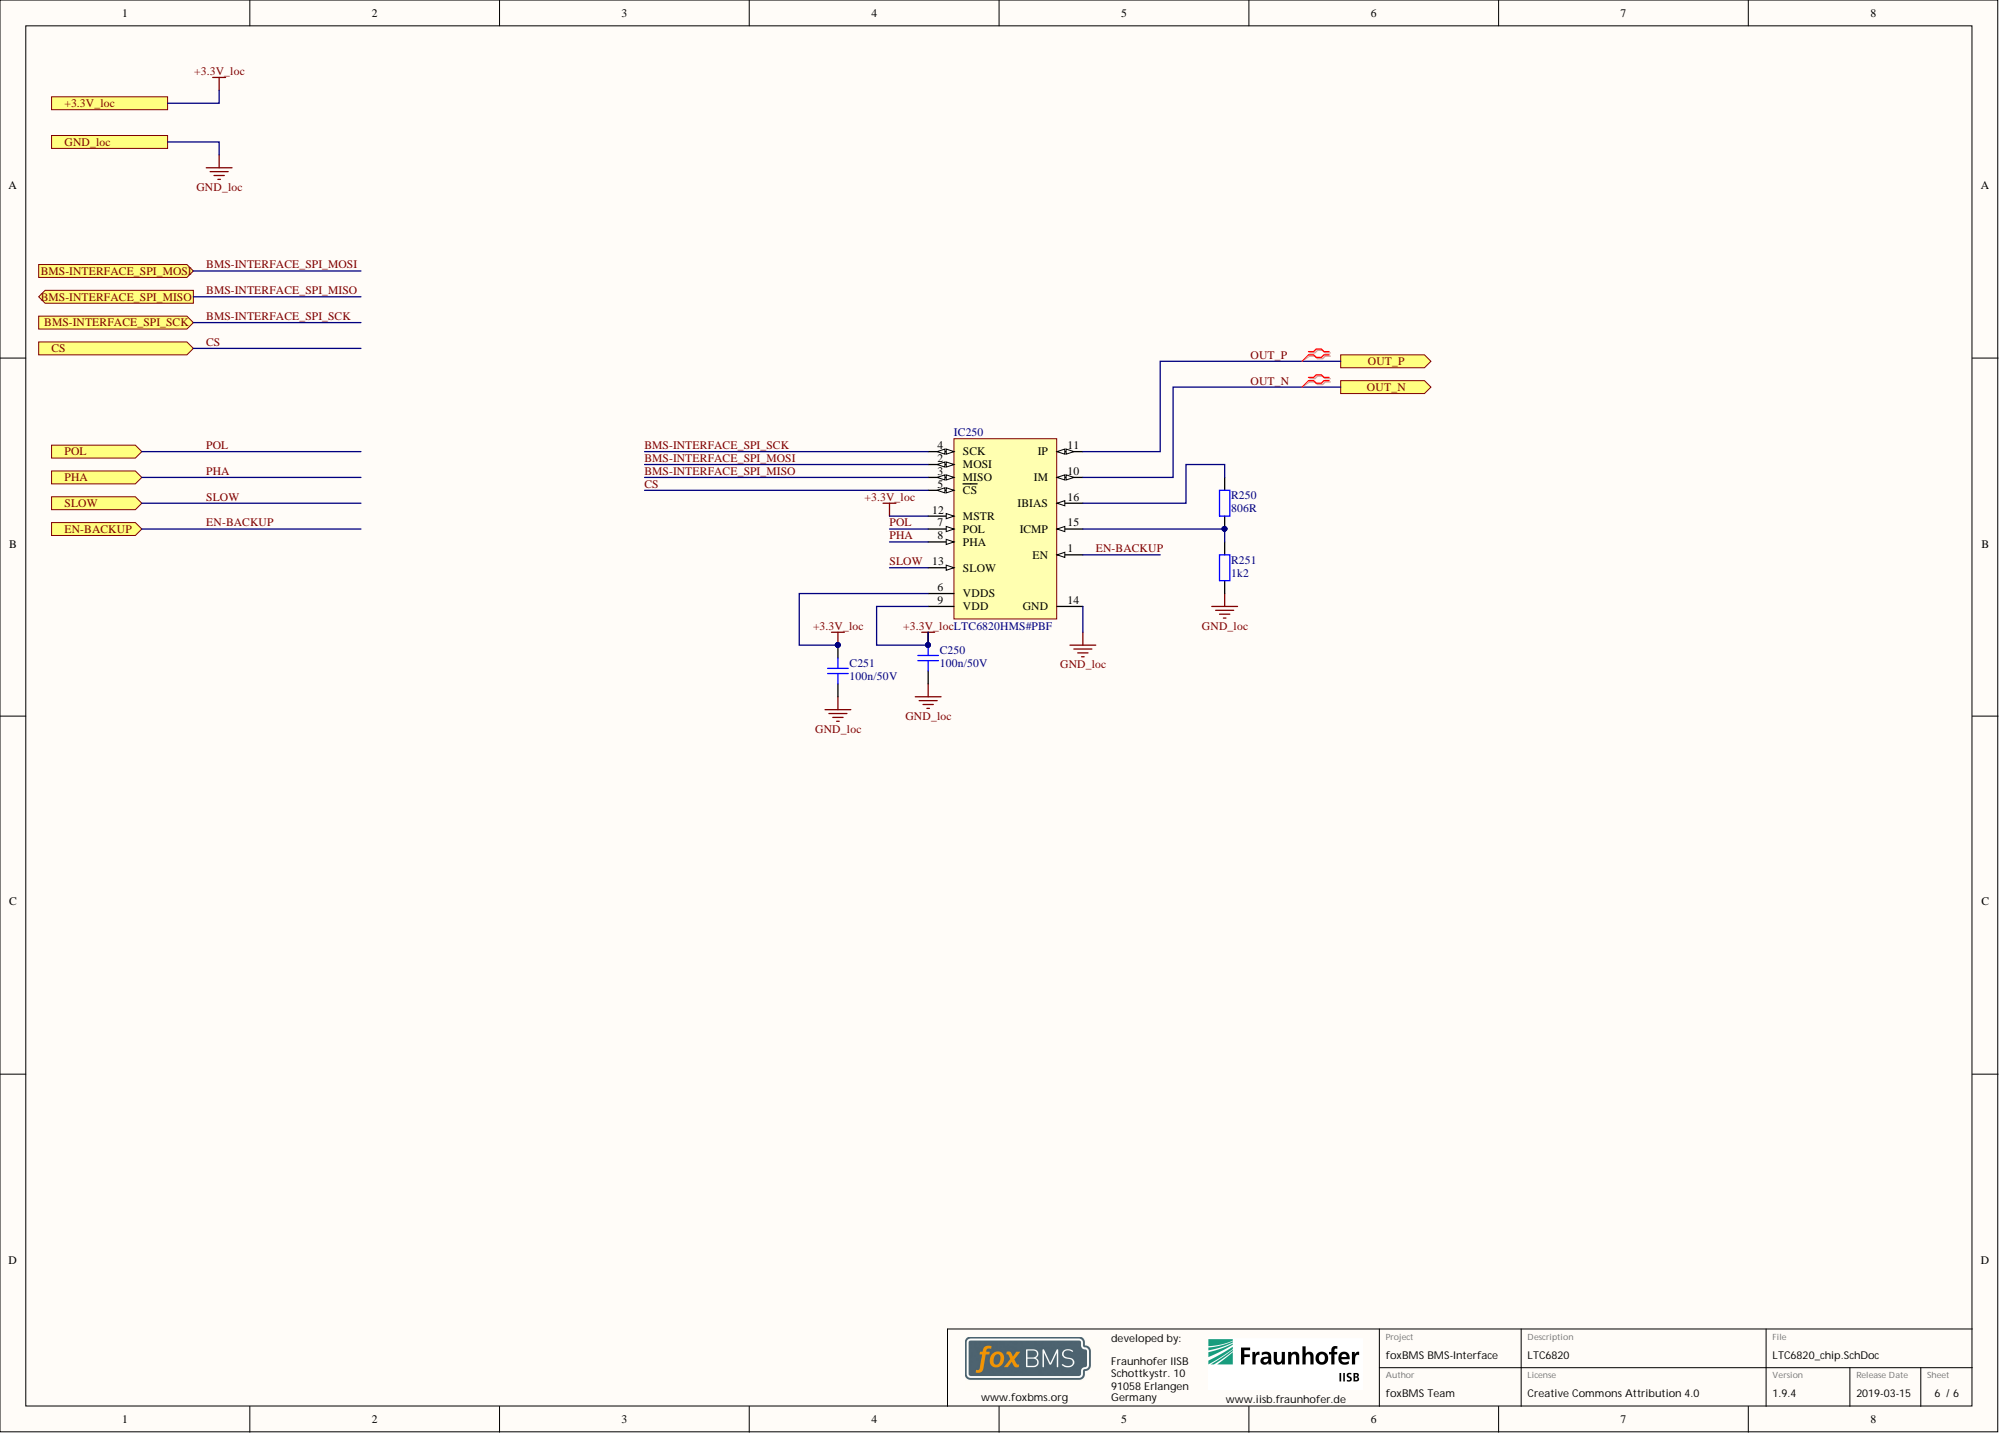
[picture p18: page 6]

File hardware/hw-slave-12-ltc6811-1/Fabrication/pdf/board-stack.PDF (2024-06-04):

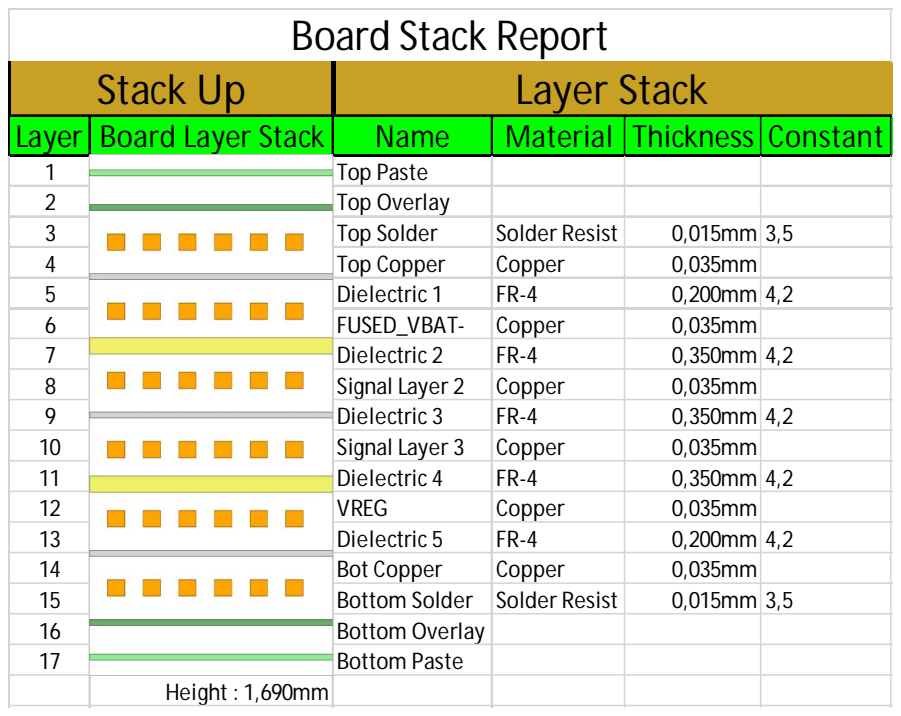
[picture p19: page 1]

Stack Up | Layer Stack
Layer | Board Layer Stack | Name | Material | Thickness | Constant
1 | | Top Paste
2 | | Top Overlay
3 | | Top Solder | Solder Resist | 0,015mm | 3,5
4 | | Top Copper | Copper | 0,035mm
5 | | Dielectric 1 | FR-4 | 0,200mm | 4,2
6 | | FUSED_VBAT- | Copper | 0,035mm
7 | | Dielectric 2 | FR-4 | 0,350mm | 4,2
8 | | Signal Layer 2 | Copper | 0,035mm
9 | | Dielectric 3 | FR-4 | 0,350mm | 4,2
10 | | Signal Layer 3 | Copper | 0,035mm
11 | | Dielectric 4 | FR-4 | 0,350mm | 4,2
12 | | VREG | Copper | 0,035mm
13 | | Dielectric 5 | FR-4 | 0,200mm | 4,2
14 | | Bot Copper | Copper | 0,035mm
15 | | Bottom Solder | Solder Resist | 0,015mm | 3,5
16 | | Bottom Overlay
17 | | Bottom Paste

Height : 1,690mm

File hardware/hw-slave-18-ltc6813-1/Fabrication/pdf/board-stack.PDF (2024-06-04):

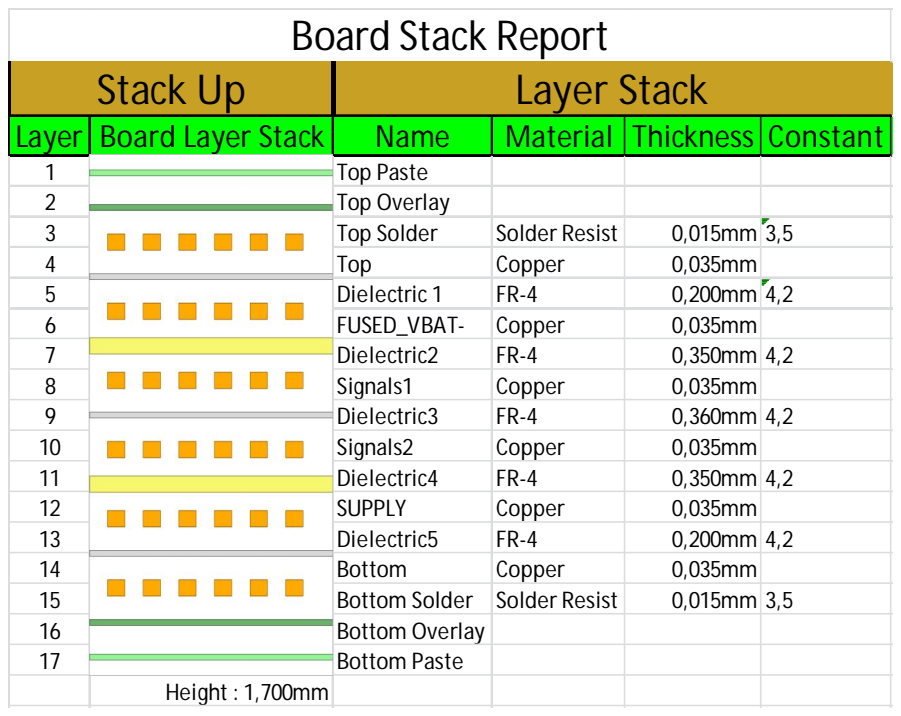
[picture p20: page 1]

Stack Up | Layer Stack
Layer | Board Layer Stack | Name | Material | Thickness | Constant
1 | | Top Paste
2 | | Top Overlay
3 | | Top Solder | Solder Resist | 0,015mm | 3,5
4 | | Top | Copper | 0,035mm
5 | | Dielectric 1 | FR-4 | 0,200mm | 4,2
6 | | FUSED_VBAT- | Copper | 0,035mm
7 | | Dielectric2 | FR-4 | 0,350mm | 4,2
8 | | Signals1 | Copper | 0,035mm
9 | | Dielectric3 | FR-4 | 0,360mm | 4,2
10 | | Signals2 | Copper | 0,035mm
11 | | Dielectric4 | FR-4 | 0,350mm | 4,2
12 | | SUPPLY | Copper | 0,035mm
13 | | Dielectric5 | FR-4 | 0,200mm | 4,2
14 | | Bottom | Copper | 0,035mm
15 | | Bottom Solder | Solder Resist | 0,015mm | 3,5
16 | | Bottom Overlay
17 | | Bottom Paste

Height : 1,700mm

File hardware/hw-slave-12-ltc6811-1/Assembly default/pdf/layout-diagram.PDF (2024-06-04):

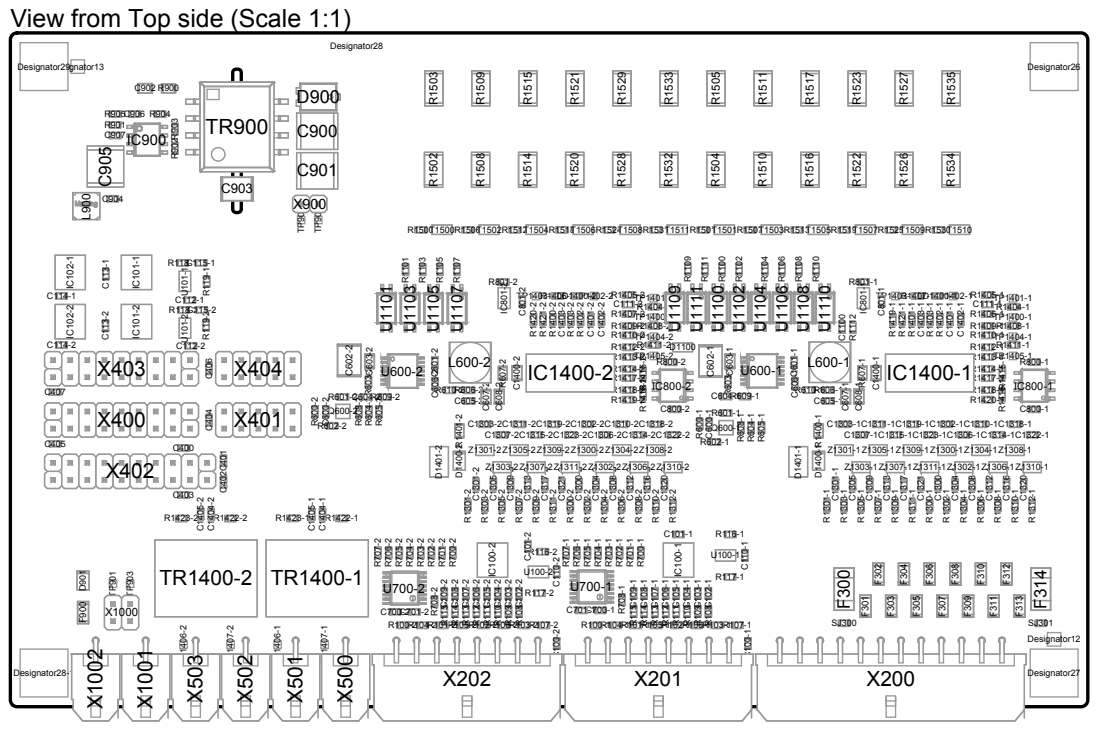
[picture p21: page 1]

View from Top side (Scale 1:1)

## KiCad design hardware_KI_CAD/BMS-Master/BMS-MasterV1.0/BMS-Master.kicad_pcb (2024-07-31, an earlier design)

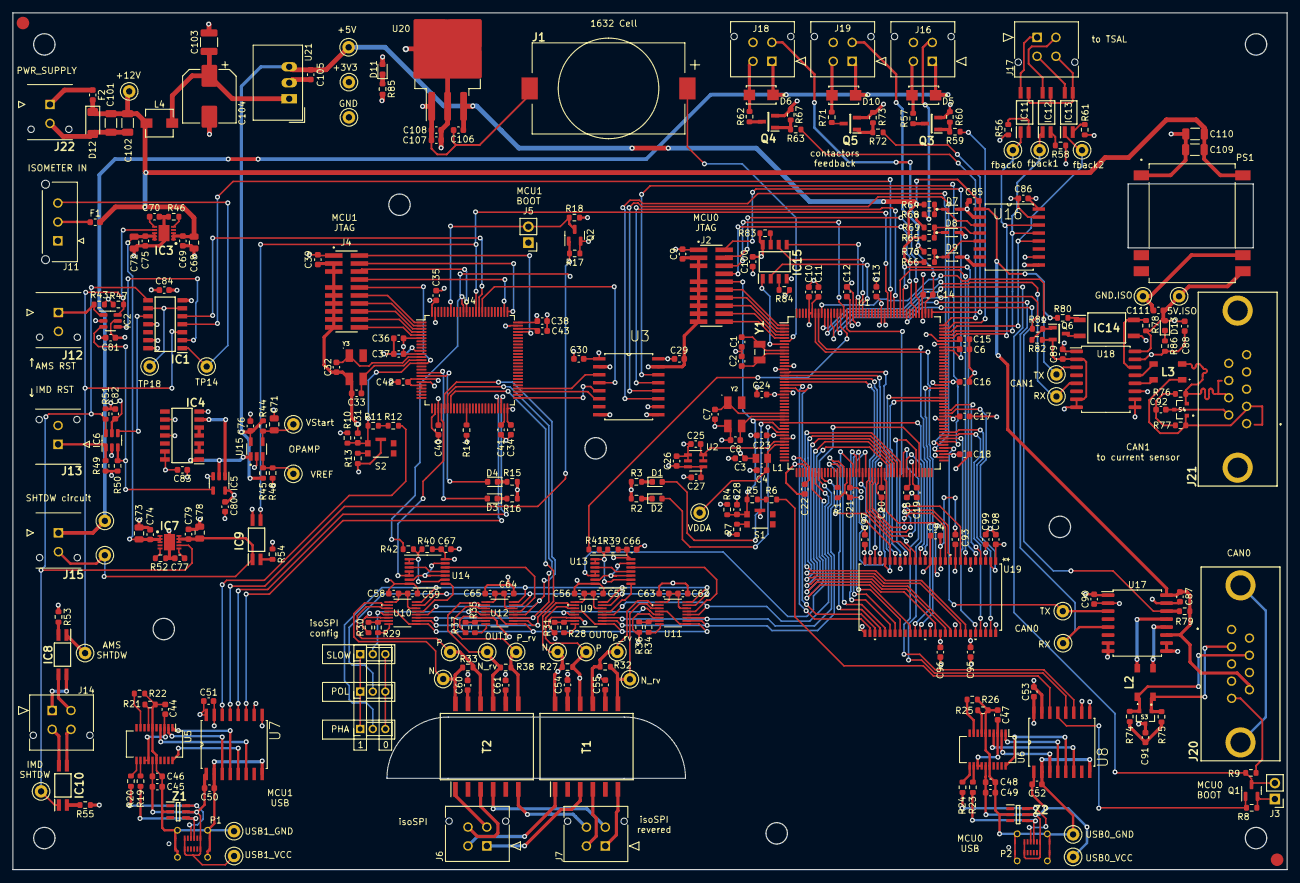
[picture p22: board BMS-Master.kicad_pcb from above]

Board: 4 copper layers, 202.7 x 136.3 mm, 330 parts (0 on the bottom side), 281 nets.

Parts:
C1, C2, C7, C8, C32, C33: 18pF/50V; C_0603_1608Metric
C3, C4, C9, C10, C11, C12, C13, C14, C15, C16, C17, C18, C19, C20, C21, C22, C23, C24, C25, C27, C28, C29, C30, C31, C34, C35, C36, C37, C38, C39, C40, C42, C70, C77, C85, C86, C87, C88, C89, C90, C105, C106, C108, C111: 100nF/50V; C_0603_1608Metric
C5, C6, C41, C43: 2u2/10V; C_0603_1608Metric
C26, C91, C92, C107: 1uF/35V; C_0603_1608Metric
C44, C46, C47, C49, C50, C51, C52, C53, C56, C57, C58, C59, C62, C63, C64, C65, C66, C67, C76, C80, C81, C82, C83, C84, C93, C94, C95, C96, C97, C98, C99, C100: 100n/50V; C_0603_1608Metric
C45, C48: 4u7/25V; C_0603_1608Metric
C54, C55, C60, C61: 27pF/50V; C_0603_1608Metric
C68, C72, C73, C78: 10u/50V; C_0805_2012Metric
C69, C74, C75, C79: 0.1u/50V; C_0603_1608Metric
C71: 68uF/50V; C_0805_2012Metric
C101, C102: 10uF/50V; C_1206_3216Metric
C103: 10uF/50V; C_1210_3225Metric
C104: 56uF/50V (8mm diameter); CP_Elec_8x10
C109, C110: 47uF/25V; C_1206_3216Metric
D1, D3: LED_RED; LED_0603_1608Metric
D2, D4: LED_Green; LED_0603_1608Metric
D5, D6, D10: GF1B-E3_67A; Diode_GF1B-E367A
D7, D8, D9: CDSOD323-T05; Bourns_Inc.-SOD-323-0-0-IPC_B
D11, D13: LED orange; LED_0603_1608Metric
D12: BZV55B15; D_MiniMELF
F1: 0408002.WR; Fuse_0603_1608Metric
F2: 0408007.WR; Fuse_0603_1608Metric
FID1, FID2: Fiducial; fiducial 2mm with 3mm mask
IC1: SN74LVC08AD; SOIC127P600X175-14N
IC2, IC6: SN74LVC1G332DBVR; TSOT-23-6
IC3, IC7: LS1205EF; SON50P300X300X80-11N
IC4: SN74HC04DR; SOIC127P600X175-14N
IC5: SN74LVC1G02DBVT; TSOT-23-5
IC8, IC9, IC10, IC11, IC12, IC13: ACPL-217-56BE; SOIC127P700X242-4N
IC14: AQY-211EHA; SOP254P962X315-4N
IC15: M95M02-DRMN6TP; SOIC127P600X175-8N
J1: SMTU1632-LF.TR; SMTU1632LFTR
J2, J4: FTSH-110-01-L-DV-007; SAMTEC_FTSH-110-01-L-DV-007
J3, J5: Conn_01x02_Pin; PinHeader_1x02_P2.54mm_Vertical
J6, J7, J14, J16, J17, J18, J19: 430450412; CON_430450412_MOL
J8, J9, J10: Conn_01x03_Pin; PinHeader_1x03_P2.00mm_Vertical
J11: 436500327; MOLEX_436500327
J12, J13, J15, J22: 43045-0212; 43045-02YY_121314
J20, J21: DE9_Receptacle_MountingHoles; L177TSEH09SOL2RM8
L1: BLM21AG471SN1J; IND_BLM21_0805_MUR
L2, L3: ACT45B 2000uH; ACT45B1012PTL003
L4: 5.6uH; L_TracoPower_TCK-141
P1, P2: USB_C_Plug_USB2.0; molex 2193200001
PS1: TRI_1-1211SM; CONV_TRI_1-1211SM
Q1, Q2: BSS84; SOT-23
Q3, Q4, Q5, Q6: IRLML0100TRPBF; SOT95P237X112-3N
R1, R4, R8, R9, R10, R14, R17, R18, R43, R44, R47, R48, R49, R50, R51, R60, R64, R65, R66, R67, R73, R78, R79, R82, R83, R84: 10k; R_0603_1608Metric
R2, R3, R15, R16, R53, R55, R56, R58, R61, R85: 130R; R_0603_1608Metric
R5, R11: 680R; R_0603_1608Metric
R6, R7, R12, R13, R21, R22, R25, R26, R41, R42: 0R; R_0603_1608Metric
R19, R20, R23, R24: 27R; R_0603_1608Metric
R27, R32, R33, R38: 120R; R_0603_1608Metric
R28, R29, R34, R35: 820R; R_0603_1608Metric
R30, R31, R36, R37: 1k2; R_0603_1608Metric
R39, R40: 20k; R_0603_1608Metric
R45, R57, R62, R71: 1k; R_0603_1608Metric
R46, R52: 6k8; R_0603_1608Metric
R54: 470R; R_0603_1608Metric
R59, R63, R72, R81: 10R; R_0603_1608Metric
R68, R69, R70: 47R; R_0603_1608Metric
R74, R75, R76, R77: 62R; R_0603_1608Metric
R80: 2k7; R_0603_1608Metric
R86: 200R; R_0603_1608Metric
S1, S2: KMR221GLFS; SW_KMR221GLFS
S3, S4: PESD1CAN_215; DIO_PESD1CAN_215
T1, T2: HM2102NL; SOP200P1473X500-12N
TP1, TP2, TP3, TP4, TP5, TP6, TP7, TP8, TP9, TP10, TP11, TP12, TP13, TP14, TP16, TP17, TP18, TP20, TP21, TP22, TP23, TP24, TP25, TP26, TP27, TP28, TP29, TP30, TP31, TP32, TP33, TP34, TP35, TP36: TestPoint; TestPoint_Keystone_5000-5004_Miniature
U1: STM32F429IIT6; LQFP-176_24x24mm_P0.5mm
U2: ADR3425ARJZ-R2; RJ_6_ADI
U3, U7, U8: ADUM3401CRWZ; SOIC127P1032X265-16N
U4: STM32F429VITx; LQFP-100_14x14mm_P0.5mm
U5, U6: FT231XS-R; SSOP-20_3.9x8.7mm_P0.635mm
U9, U10, U11, U12: LTC6820HMS-PBF; MS_05-08-1669_ADI
U13, U14: SN74LVC00AQPWRQ1; TSSOP-14_4.4x5mm_P0.65mm
U15: AD8628ARTZ-R2; SOT95P280X145-5N
U16: ADUM3300CRWZ; SOIC127P1032X265-16N
U17, U18: TJA1052IT/5Y; SOIC-16W_7.5x10.3mm_P1.27mm
U19: IS42S16400J-7TLI; 54L_TSOP-2_400_ISI
U20: LM1085IS-3.3/NOPB; TO-263-3_TabPin2
U21: TSR_2-2450; Converter_DCDC_TRACO_TSR-1_THT
Y1: ABS07-32.768KHZ-T; ABS07
Y2, Y3: 7B-8.000MAAJ-T; OSCSC500X320X105-4N
Z1, Z2: IP4220CZ6,125; SOT95P275X110-6N

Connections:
+3.3V: C3.1, C9.1, C10.1, C11.1, C12.1, C13.1, C14.1, C15.1, C16.1, C17.1, C18.1, C19.1, C20.1, C21.1, C22.1, C23.1, C24.1, C26.1, C27.1, C29.2, C30.2, C34.1, C35.1, C36.1, C37.1, C38.1, C39.1, C40.1, C42.1, C51.2, C53.2, C66.1, C67.1, C80.1, C81.1, C82.1, C83.1, C84.1, C86.2, C89.2, C90.2, C93.1, C94.1, C95.1, C96.1, C97.1, C98.1, C99.1, C100.1, C107.1, C108.1, D11.2 (A), IC1.14 (VCC), IC2.5 (VCC), IC4.9, IC4.11, IC4.13, IC4.14 (VCC), IC5.5 (VCC), IC6.5 (VCC), IC9.4 (C), IC15.8 (VCC), J2.01, J3.1, J4.01, J5.1, J8.1, J9.1, J10.1, J12.2, J13.2, L1.2, Q1.2 (S), Q2.2 (S), R4.1, R8.1, R10.1, R17.1, R39.1, R40.1, R83.1, R84.1, TP33.1, U1.15 (VDD), U1.23 (VDD), U1.36 (VDD), U1.49 (VDD), U1.62 (VDD), U1.72 (VDD), U1.82 (VDD), U1.91 (VDD), U1.103 (VDD), U1.114 (VDD), U1.127 (VDD), U1.136 (VDD), U1.149 (VDD), U1.159 (VDD), U1.171 (PDR_ON), U1.172 (VDD), U2.3 (ENABLE), U2.4 (VIN), U3.1 (VDD1), U3.10 (VE2), U3.16 (VDD2), U4.6 (VBAT), U4.11 (VDD), U4.19 (VDD), U4.21 (VREF+), U4.22 (VDDA), U4.28 (VDD), U4.50 (VDD), U4.75 (VDD), U4.100 (VDD), U7.10 (VE2), U7.16 (VDD2), U8.10 (VE2), U8.16 (VDD2), U9.1 (EN), U9.12 (MSTR), U10.1 (EN), U10.12 (MSTR), U11.1 (EN), U11.12 (MSTR), U12.1 (EN), U12.12 (MSTR), U13.14 (VCC), U14.14 (VCC), U16.10 (VE2), U16.16 (VDD2), U17.1 (VDD1), U18.1 (VDD1), U19.1 (VDD), U19.3 (VDDQ), U19.9 (VDDQ), U19.14 (VDD), U19.27 (VDD), U19.43 (VDDQ), U19.49 (VDDQ), U20.2 (VO)
+5V: C76.1, C85.2, C87.2, C105.1, C106.1, J20.9, R44.1, R45.1, R64.1, R65.1, R66.1, R79.2, R80.1, TP32.1, U15.5, U16.1 (VDD1), U17.11 (VDD2), U17.16 (VDD2), U20.3 (VI), U21.3 (Vout)
+5V_ISO: C88.2, C111.1, D13.2 (A), J21.9, PS1.8 (+VOUT), R78.1, TP35.1, U18.11 (VDD2), U18.16 (VDD2)
/CAN0_interface/CAN0.RX: TP29.1, U1.163 (PB5), U17.5 (RXD)
/CAN0_interface/CAN0.TRANS_STBY_CTRL: R79.1, U1.141 (PC12), U17.14 (STB)
/CAN0_interface/CAN0.TX: TP27.1, U1.93 (PB13), U17.3 (TXD)
/CAN0_interface/CAN0_H: J20.7, L2.1, R74.1, S3.2
/CAN0_interface/CAN0_L: J20.2, L2.2, R75.1, S3.1
/CAN0_interface/CAN1.RX: TP30.1, U1.167 (PB8), U18.5 (RXD)
/CAN0_interface/CAN1.TRANS_STBY_CTRL: R81.2, U1.165 (PB7)
/CAN0_interface/CAN1.TX: TP28.1, U1.168 (PB9), U18.3 (TXD)
/CAN0_interface/CAN1_+: J21.7, L3.2, R76.1, S4.2
/CAN0_interface/CAN1_-: J21.2, L3.1, R77.1, S4.1
/Contactors/Contactor_ctrl0: R59.1, U1.131 (PI0)
/Contactors/Contactor_ctrl1: R63.1, U1.132 (PI1)
/Contactors/Contactor_ctrl2: R72.1, U1.133 (PI2)
/Contactors/Contactor_feedback0: IC11.1 (A), TP24.1, U1.128 (PH13), U16.14 (VOA)
/Contactors/Contactor_feedback1: IC12.1 (A), TP25.1, U1.129 (PH14), U16.13 (VOB)
/Contactors/Contactor_feedback2: IC13.1 (A), TP26.1, U1.130 (PH15), U16.12 (VOC)
/Contactors/Contactor_out0: D5.2 (ANODE), J16.2, R57.1
/Contactors/Contactor_out1: D6.2 (ANODE), J18.2, R62.1
/Contactors/Contactor_out2: D10.2 (ANODE), J19.2, R71.1
/Contactors/contactors_com_pos: D5.1 (CATHODE), D6.1 (CATHODE), D10.1 (CATHODE), J15.1, J16.1, J18.1, J19.1, TP23.1
/Contactors/feedback0: J16.3, R68.1
/Contactors/feedback1: J18.3, R69.1
/Contactors/feedback2: J19.3, R70.1
/MCU0_Memory/EEPROM.CS: IC15.1 (~S), U1.7 (PI8)
/MCU0_Memory/EEPROM.MISO: IC15.2 (Q), U1.155 (PG12)
/MCU0_Memory/EEPROM.MOSI: IC15.5 (D), U1.157 (PG14)
/MCU0_Memory/EEPROM.SCK: IC15.6 (C), U1.156 (PG13)
/MCU0_Memory/MCU0_RAM.A0: U1.16 (PF0), U19.23 (A0)
/MCU0_Memory/MCU0_RAM.A1: U1.17 (PF1), U19.24 (A1)
/MCU0_Memory/MCU0_RAM.A2: U1.18 (PF2), U19.25 (A2)
/MCU0_Memory/MCU0_RAM.A3: U1.19 (PF3), U19.26 (A3)
/MCU0_Memory/MCU0_RAM.A4: U1.20 (PF4), U19.29 (A4)
/MCU0_Memory/MCU0_RAM.A5: U1.21 (PF5), U19.30 (A5)
/MCU0_Memory/MCU0_RAM.A6: U1.60 (PF12), U19.31 (A6)
/MCU0_Memory/MCU0_RAM.A7: U1.63 (PF13), U19.32 (A7)
/MCU0_Memory/MCU0_RAM.A8: U1.64 (PF14), U19.33 (A8)
/MCU0_Memory/MCU0_RAM.A9: U1.65 (PF15), U19.34 (A9)
/MCU0_Memory/MCU0_RAM.A10: U1.66 (PG0), U19.22 (A10)
/MCU0_Memory/MCU0_RAM.A11: U1.67 (PG1), U19.35 (A11)
/MCU0_Memory/MCU0_RAM.BA0: U1.108 (PG4), U19.20 (BA0)
/MCU0_Memory/MCU0_RAM.BA1: U1.109 (PG5), U19.21 (BA1)
/MCU0_Memory/MCU0_RAM.D0: U1.104 (PD14), U19.2 (DQ0)
/MCU0_Memory/MCU0_RAM.D1: U1.105 (PD15), U19.4 (DQ1)
/MCU0_Memory/MCU0_RAM.D2: U1.142 (PD0), U19.5 (DQ2)
/MCU0_Memory/MCU0_RAM.D3: U1.143 (PD1), U19.7 (DQ3)
/MCU0_Memory/MCU0_RAM.D4: U1.68 (PE7), U19.8 (DQ4)
/MCU0_Memory/MCU0_RAM.D5: U1.69 (PE8), U19.10 (DQ5)
/MCU0_Memory/MCU0_RAM.D6: U1.70 (PE9), U19.11 (DQ6)
/MCU0_Memory/MCU0_RAM.D7: U1.73 (PE10), U19.13 (DQ7)
/MCU0_Memory/MCU0_RAM.D8: U1.74 (PE11), U19.42 (DQ8)
/MCU0_Memory/MCU0_RAM.D9: U1.75 (PE12), U19.44 (DQ9)
/MCU0_Memory/MCU0_RAM.D10: U1.76 (PE13), U19.45 (DQ10)
/MCU0_Memory/MCU0_RAM.D11: U1.77 (PE14), U19.47 (DQ11)
/MCU0_Memory/MCU0_RAM.D12: U1.78 (PE15), U19.48 (DQ12)
/MCU0_Memory/MCU0_RAM.D13: U1.96 (PD8), U19.50 (DQ13)
/MCU0_Memory/MCU0_RAM.D14: U1.97 (PD9), U19.51 (DQ14)
/MCU0_Memory/MCU0_RAM.D15: U1.98 (PD10), U19.53 (DQ15)
/MCU0_Memory/MCU0_RAM.NBL0: U1.169 (PE0), U19.15 (LDQM)
/MCU0_Memory/MCU0_RAM.NBL1: U1.170 (PE1), U19.39 (UDQM)
/MCU0_Memory/MCU0_RAM.SDCKE1: U1.84 (PH7), U19.37 (CKE)
/MCU0_Memory/MCU0_RAM.SDCLK: U1.112 (PG8), U19.38 (CLK)
/MCU0_Memory/MCU0_RAM.SDNCAS: U1.160 (PG15), U19.17 (CAS)
/MCU0_Memory/MCU0_RAM.SDNE1: U1.83 (PH6), U19.19 (CS)
/MCU0_Memory/MCU0_RAM.SDNRAS: U1.59 (PF11), U19.18 (RAS)
/MCU0_Memory/MCU0_RAM.SDNWE: U1.32 (PC0), U19.16 (WE)
/MCU0_primary/FTDI_MCU0.DTR: Q1.1 (G), R8.2, U8.13 (VOB)
/MCU0_primary/FTDI_MCU0.RTS: R6.2, U8.14 (VOA)
/MCU0_primary/FTDI_MCU0.RX: U1.80 (PB11), U8.12 (VOC)
/MCU0_primary/FTDI_MCU0.TX: U1.79 (PB10), U8.11 (VID)
/MCU0_primary/MCU0_ADC_REF/VREF+_MCU0: C25.1, U1.38 (VREF+), U2.5 (VOUTSENSE), U2.6 (VOUTFORCE)
/MCU0_primary/MCU0_BOOT: J3.2, Q1.3 (D), R9.1, U1.166 (BOOT0)
/MCU0_primary/MCU0_NRST: C28.1, J2.10, R4.2, R5.1, S1.1, U1.31 (NRST)
/MCU0_primary/MCU0_SWCLK: J2.04, U1.137 (PA14)
/MCU0_primary/MCU0_SWDIO: J2.02, U1.124 (PA13)
/MCU0_primary/MCU0_SWO: J2.06, U1.161 (PB3)
/MCU0_primary/MCU0_TDI: J2.08, U1.138 (PA15)
/MCU0_primary/MCU0_TRACECLK: J2.12, U1.1 (PE2)
/MCU0_primary/MCU0_TRACED0: J2.14, U1.2 (PE3)
/MCU0_primary/MCU0_TRACED1: J2.16, U1.3 (PE4)
/MCU0_primary/MCU0_TRACED2: J2.18, U1.4 (PE5)
/MCU0_primary/MCU0_TRACED3: J2.20, U1.5 (PE6)
/MCU0_primary/MCU_to_MCU_INTERFACE_MCU0.CS: U1.92 (PB12), U3.12 (VOC)
/MCU0_primary/MCU_to_MCU_INTERFACE_MCU0.MISO: U1.94 (PB14), U3.11 (VID)
/MCU0_primary/MCU_to_MCU_INTERFACE_MCU0.MOSI: U1.95 (PB15), U3.14 (VOA)
/MCU0_primary/MCU_to_MCU_INTERFACE_MCU0.SCK: U1.145 (PD3), U3.13 (VOB)
/MCU0_primary/SHUTDOWN_ctrl_MCU0: IC1.4, U1.146 (PD4)
/MCU0_primary/SHUTDOWN_feedback_MCU0: IC9.3 (E), U1.147 (PD5), U4.86 (PD5)
/MCU0_primary/isoSPI0.CS: U1.50 (PA4), U13.4, U13.5
/MCU0_primary/isoSPI0.DIR: R41.1, U1.162 (PB4)
/MCU0_primary/isoSPI0.MISO: U1.52 (PA6), U9.3 (MISO), U11.3 (MISO)
/MCU0_primary/isoSPI0.MOSI: U1.53 (PA7), U9.2 (MOSI), U11.2 (MOSI)
/MCU0_primary/isoSPI0.SCK: U1.51 (PA5), U9.4 (SCK), U11.4 (SCK)
/MCU1_secondary/FTDI_MCU1.DTR: Q2.1 (G), R17.2, U7.13 (VOB)
/MCU1_secondary/FTDI_MCU1.RTS: R12.2, U7.14 (VOA)
/MCU1_secondary/FTDI_MCU1.RX: U4.48 (PB11), U7.12 (VOC)
/MCU1_secondary/FTDI_MCU1.TX: U4.47 (PB10), U7.11 (VID)
/MCU1_secondary/MCU1_BOOT: J5.2, Q2.3 (D), R18.1, U4.94 (BOOT0)
/MCU1_secondary/MCU1_NRST: C31.1, J4.10, R10.2, R11.1, S2.1, U4.14 (NRST)
/MCU1_secondary/MCU1_SWCLK: J4.04, U4.76 (PA14)
/MCU1_secondary/MCU1_SWDIO: J4.02, U4.72 (PA13)
/MCU1_secondary/MCU1_SWO: J4.06, U4.89 (PB3)
/MCU1_secondary/MCU1_TDI: J4.08, U4.77 (PA15)
/MCU1_secondary/MCU1_TRACECLK: J4.12, U4.1 (PE2)
/MCU1_secondary/MCU1_TRACED0: J4.14, U4.2 (PE3)
/MCU1_secondary/MCU1_TRACED1: J4.16, U4.3 (PE4)
/MCU1_secondary/MCU1_TRACED2: J4.18, U4.4 (PE5)
/MCU1_secondary/MCU1_TRACED3: J4.20, U4.5 (PE6)
/MCU1_secondary/MCU_to_MCU_INTERFACE_MCU1.CS: U3.5 (VIC), U4.51 (PB12)
/MCU1_secondary/MCU_to_MCU_INTERFACE_MCU1.MISO: U3.6 (VOD), U4.53 (PB14)
/MCU1_secondary/MCU_to_MCU_INTERFACE_MCU1.MOSI: U3.3 (VIA), U4.54 (PB15)
/MCU1_secondary/MCU_to_MCU_INTERFACE_MCU1.SCK: U3.4 (VIB), U4.84 (PD3)
/MCU1_secondary/SHUTDOWN_ctrl_MCU0: IC1.5, U4.85 (PD4)
/MCU1_secondary/isoSPI1.CS: U4.29 (PA4), U14.4, U14.5
/MCU1_secondary/isoSPI1.DIR: R42.1, U4.90 (PB4)
/MCU1_secondary/isoSPI1.MISO: U4.31 (PA6), U10.3 (MISO), U12.3 (MISO)
/MCU1_secondary/isoSPI1.MOSI: U4.32 (PA7), U10.2 (MOSI), U12.2 (MOSI)
/MCU1_secondary/isoSPI1.SCK: U4.30 (PA5), U10.4 (SCK), U12.4 (SCK)
/Shutdown/AMS_SHTDW: IC1.3, IC2.6, IC3.7 (EN), IC8.1 (A), R47.2, TP20.1
/Shutdown/Bender_OK_EXT: IC1.1, J11.3, TP14.1
/Shutdown/IMD_SHTDW: IC1.8, IC6.6, IC7.7 (EN), IC10.1 (A), R51.2, TP21.1
/USB_interface/D0+: P2.A6 (D+), R24.1, Z2.6 (I/O_4)
/USB_interface/D0-: P2.A7 (D-), R23.1, Z2.4 (I/O_3)
/USB_interface/D1+: P1.A6 (D+), R20.1, Z1.6 (I/O_4)
/USB_interface/D1-: P1.A7 (D-), R19.1, Z1.4 (I/O_3)
/USB_interface/USB_MCU0.DTR: U6.1 (~DTR), U8.4 (VIB)
/USB_interface/USB_MCU0.RTS: U6.2 (~RTS), U8.3 (VIA)
/USB_interface/USB_MCU0.RX: U6.4 (RXD), U8.6 (VOD)
/USB_interface/USB_MCU0.TX: U6.20 (TXD), U8.5 (VIC)
/USB_interface/USB_MCU1.DTR: U5.1 (~DTR), U7.4 (VIB)
/USB_interface/USB_MCU1.RTS: U5.2 (~RTS), U7.3 (VIA)
/USB_interface/USB_MCU1.RX: U5.4 (RXD), U7.6 (VOD)
/USB_interface/USB_MCU1.TX: U5.20 (TXD), U7.5 (VIC)
/isoSPI_interface/CS0_F: U9.5 (*CS), U13.8
/isoSPI_interface/CS0_rv: U11.5 (*CS), U13.12
/isoSPI_interface/CS1_F: U10.5 (*CS), U14.8
/isoSPI_interface/CS1_rv: U12.5 (*CS), U14.12
/isoSPI_interface/OUT0_N: R27.1, T1.12 (SEC_6), TP7.1, U9.10 (IM)
/isoSPI_interface/OUT0_N_rv: R32.2, T1.9 (SEC_3), TP8.1, U11.10 (IM)
/isoSPI_interface/OUT0_P: R27.2, T1.10 (SEC_4), TP6.1, U9.11 (IP)
/isoSPI_interface/OUT0_P_rv: R32.1, T1.7 (SEC_1), TP9.1, U11.11 (IP)
/isoSPI_interface/OUT1_N: R33.1, T2.12 (SEC_6), TP11.1, U10.10 (IM)
/isoSPI_interface/OUT1_N_rv: R38.2, T2.9 (SEC_3), TP12.1, U12.10 (IM)
/isoSPI_interface/OUT1_P: R33.2, T2.10 (SEC_4), TP10.1, U10.11 (IP)
/isoSPI_interface/OUT1_P_rv: R38.1, T2.7 (SEC_1), TP13.1, U12.11 (IP)
/isoSPI_interface/PHA_0: J9.2, U9.8 (PHA), U10.8 (PHA), U11.8 (PHA), U12.8 (PHA)
/isoSPI_interface/POL_0: J8.2, U9.7 (POL), U10.7 (POL), U11.7 (POL), U12.7 (POL)
/isoSPI_interface/SLOW: J10.2, U9.13 (SLOW), U10.13 (SLOW), U11.13 (SLOW), U12.13 (SLOW)
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

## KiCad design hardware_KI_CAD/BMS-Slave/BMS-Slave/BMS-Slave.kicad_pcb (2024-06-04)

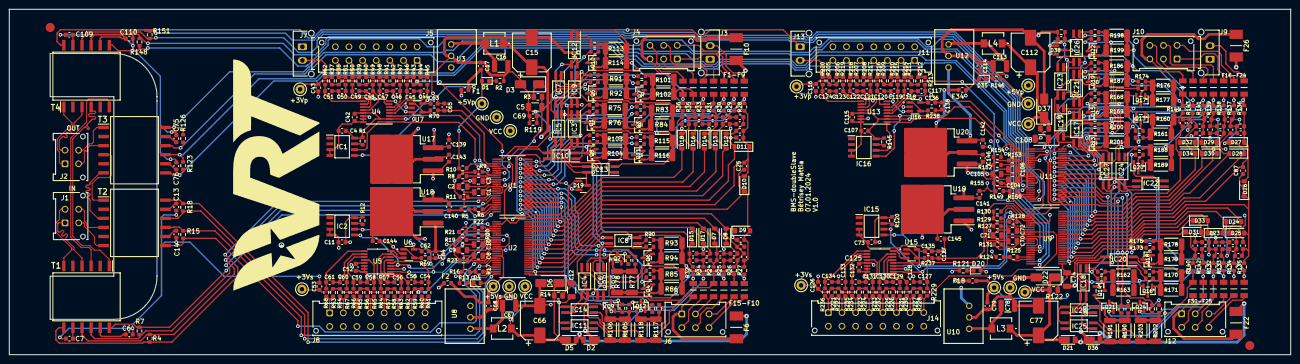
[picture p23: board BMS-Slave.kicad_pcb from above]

Board: 4 copper layers, 282.0 x 76.0 mm, 568 parts (0 on the bottom side), 360 nets.

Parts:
C1, C2, C3, C8, C9, C10, C70, C71, C72, C104, C105, C106: 1uF/50V; C_0805_2012Metric
C4, C11, C17, C43, C53, C68, C73, C79, C107, C114, C116, C126, C139, C140, C141, C142: 100nF/50V; C_0603_1608Metric
C5, C12, C74, C108: 100nF/200V; C_1206_3216Metric
C6, C7, C13, C14, C75, C76, C109, C110: 100pF/50V; C_0603_1608Metric
C15, C66, C77, C112: 33uF/100V (8mm diameter); CP_Elec_8x10
C16, C67, C78, C113: 2.2uF/100V; C_1210_3225Metric
C18, C19, C20, C21, C22, C23, C24, C25, C26, C27, C28, C29, C30, C31, C32, C33, C34, C35, C36, C37, C38, C39, C40, C41, C44, C45, C46, C47, C48, C49, C50, C51, C54, C55, C56, C57, C58, C59, C60, C61, C64, C65, C80, C81, C82, C83, C84, C85, C86, C87, C88, C89, C90, C91, C92, C93, C94, C95, C96, C97, C98, C99, C100, C101, C102, C103, C117, C118, C119, C120, C121, C122, C123, C124, C127, C128, C129, C130, C131, C132, C133, C134, C137, C138: 10nF/100V; C_0603_1608Metric
C42, C52, C62, C63, C115, C125, C135, C136, C143, C144, C145, C146: 1uF/50V; C_0603_1608Metric
C69, C111: 10nF/50V; C_0603_1608Metric
D1, D4, D20, D35: LED Green TLMG1100-GS08; LED_0603_1608Metric
D2, D5, D21, D36: DFLS1100-7; POWERDI123_1
D3, D6, D22, D37: SMAJ54A-E3/61; D_SMA
D7, D8, D9, D10, D11, D12, D13, D14, D15, D16, D17, D18, D23, D24, D25, D26, D27, D28, D29, D30, D31, D32, D33, D34: SZMMSZ4692T1G; D_SOD-123
D19, D38: BAT54C,215; SOT-23
F1, F2, F18, F34: SF-0603SP063-2; Fuse_0603_1608Metric
F3, F4, F5, F7, F8, F9, F11, F12, F13, F14, F15, F16, F17, F19, F20, F21, F23, F24, F25, F27, F28, F29, F30, F31, F32, F33: 0466.250NR; FUSC3215X66N
F6, F10, F22, F26: 0448.500MR; FUSC6127X294N
FID1, FID2: Fiducial; fiducial 2mm with 3mm mask
IC1, IC2, IC15, IC16: M24M02-DWMN3TP_K; SOIC127P600X175-8N
IC3, IC4, IC5, IC6, IC7, IC8, IC9, IC10, IC11, IC12, IC13, IC14, IC17, IC18, IC19, IC20, IC21, IC22, IC23, IC24, IC25, IC26, IC27, IC28: ACPL-217-56BE; SOIC127P700X242-4N
J1, J2: 430450412; Molex_Micro-Fit_3.0_43045-0412_2x02_P3.00mm_Vertical
J3, J7, J9, J13: 43045-0212; Molex_Micro-Fit_3.0_43650-0215_1x02_P3.00mm_Vertical
J4, J6, J10, J12: Conn_01x06_Pin; Molex_Micro-Fit_3.0_43045-0612_2x03_P3.00mm_Vertical
J5, J11: Conn_01x14_Pin; Molex_Micro-Fit_3.0_43045-1412_2x07_P3.00mm_Vertical
J8, J14: Conn_01x16_Pin; Molex_Micro-Fit_3.0_43045-1612_2x08_P3.00mm_Vertical
L1, L2, L3, L4: 4.7uH; TCK176
Q1, Q2, Q3, Q4, Q5, Q6, Q7, Q8, Q9, Q10, Q11, Q12, Q13, Q14, Q15, Q16, Q17, Q18, Q19, Q20, Q21, Q22, Q23, Q24: NX2301P_215; SOT23_TO-236AB_NEX
R1, R10, R12, R21, R22, R37, R38, R39, R40, R41, R42, R43, R44, R53, R54, R55, R56, R57, R58, R59, R60, R119, R120, R129, R130, R145, R154, R204, R205, R206, R207, R208, R209, R210, R211, R212, R221, R222, R223, R224, R225, R226, R227, R228: 10k; R_0603_1608Metric
R2, R13, R121, R146: 270R; R_0603_1608Metric
R3, R14, R122, R147: 100R; R_0805_2012Metric
R4, R7, R15, R18, R123, R126, R148, R151: 120R; R_0603_1608Metric
R5, R8, R9, R16, R19, R20, R124, R127, R128, R149, R152, R153: 1k2; R_0603_1608Metric
R6, R17, R125, R150: 820R; R_0603_1608Metric
R11, R23, R131, R155: 1M; R_0603_1608Metric
R24, R25, R26, R27, R28, R29, R30, R31, R32, R33, R34, R35, R36, R45, R46, R47, R48, R49, R50, R51, R52, R61, R62, R63, R64, R65, R66, R67, R68, R69, R70, R132, R133, R134, R135, R136, R137, R138, R139, R140, R141, R142, R143, R144, R213, R214, R215, R216, R217, R218, R219, R220, R229, R230, R231, R232, R233, R234, R235, R236, R237, R238: 100R; R_0603_1608Metric
R71, R72, R79, R80, R87, R88, R95, R96, R97, R107, R108, R109, R156, R157, R164, R165, R172, R173, R180, R181, R182, R192, R193, R194: 3k3; R_0603_1608Metric
R73, R74, R81, R82, R89, R90, R98, R99, R100, R110, R111, R112, R158, R159, R166, R167, R174, R175, R183, R184, R185, R195, R196, R197: 150R; R_0603_1608Metric
R75, R76, R77, R78, R83, R84, R85, R86, R91, R92, R93, R94, R101, R102, R103, R104, R105, R106, R113, R114, R115, R116, R117, R118, R160, R161, R162, R163, R168, R169, R170, R171, R176, R177, R178, R179, R186, R187, R188, R189, R190, R191, R198, R199, R200, R201, R202, R203: 68R 1/3W; R_2010_5025Metric
T1, T2, T3, T4: HM2102NL; SOP200P1473X500-12N
TP1, TP2, TP3, TP4, TP5, TP6, TP7, TP8, TP9, TP10, TP11, TP12, TP13, TP14, TP15, TP16: TestPoint; TestPoint_Keystone_5000-5004_Miniature
U1, U2, U9, U11: LTC6811HG-1_PBF; SOP50P780X200-48N
U3, U8, U10, U12: TSR 0.6-4890WI; TSR 0.6-4850WI
U4, U5, U13, U14: ADG728BRUZ; TSSOP-16_4.4x5mm_P0.65mm
U6, U7, U15, U16: AD8628ARTZ-R2; SOT95P280X145-5N
U17, U18, U19, U20: LM1086ISX-5.0/NOPB; TO-263-3_TabPin2

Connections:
/slave1_of_2/EXT_DC_ISO_prim: C15.1, D2.1 (K), D3.1 (A1), L1.1, R3.1, TP4.1
/slave1_of_2/EXT_DC_ISO_sec: C66.1, D5.1 (K), D6.1 (A1), L2.1, R14.1, TP7.1
/slave1_of_2/GND: C1.2, C2.2, C3.2, C4.2, C5.2, C6.2, C7.2, C8.2, C9.2, C10.2, C11.2, C12.2, C13.2, C14.2, C15.2, C16.2, C17.1, C18.2, C20.2, C22.2, C24.2, C26.2, C28.2, C30.2, C32.2, C34.2, C36.2, C38.2, C40.2, C42.2, C43.2, C44.1, C45.1, C46.1, C47.1, C48.1, C49.1, C50.1, C51.1, C52.2, C53.2, C54.1, C55.1, C56.1, C57.1, C58.1, C59.1, C60.1, C61.1, C62.2, C63.2, C64.2, C65.2, C66.2, C67.2, C68.1, C69.2, C139.1, C140.1, C143.1, C144.1, D3.2 (A2), D6.2 (A2), F10.2, IC1.3 (E2), IC1.4 (VSS), IC2.3 (E2), IC2.4 (VSS), J5.8, J5.9, J5.10, J5.11, J5.12, J5.13, J5.14, J7.1, J8.9, J8.10, J8.11, J8.12, J8.13, J8.14, J8.15, J8.16, R2.2, R5.2, R13.2, R16.2, R119.2, TP5.1, TP8.1, U1.30 (V-), U1.31 (V-__1), U2.30 (V-), U2.31 (V-__1), U2.36 (DTEN), U3.2 (GND), U4.14 (GND), U4.15 (A1), U4.16 (A0), U5.14 (GND), U5.15 (A1), U5.16 (A0), U6.2, U7.2, U8.2 (GND), U17.1 (GND), U18.1 (GND)
/slave1_of_2/SCL1: IC1.6 (SCL), R8.2, U1.33 (GPIO5), U4.1 (SCL)
/slave1_of_2/SCL2: IC2.6 (SCL), R19.2, U2.33 (GPIO5), U5.1 (SCL)
/slave1_of_2/SDA1: IC1.5 (SDA), R9.2, U1.32 (GPIO4), U4.3 (SDA)
/slave1_of_2/SDA2: IC2.5 (SDA), R20.2, U2.32 (GPIO4), U5.3 (SDA)
/slave1_of_2/Temp_MUX_prim: C65.1, R70.2, U1.27 (GPIO1)
/slave1_of_2/Temp_MUX_sec: C64.1, R69.2, U2.27 (GPIO1)
/slave1_of_2/U_Analog_IN/OPA_TEMP_prim: U4.8 (D), U7.3
/slave1_of_2/U_Analog_IN/OPA_TEMP_sec: U5.8 (D), U6.3
/slave1_of_2/U_Analog_IN/T_sens0: J5.1, R44.2, R45.1
/slave1_of_2/U_Analog_IN/T_sens1: J5.2, R43.2, R46.1
/slave1_of_2/U_Analog_IN/T_sens2: J5.3, R42.2, R47.1
/slave1_of_2/U_Analog_IN/T_sens3: J5.4, R41.2, R48.1
/slave1_of_2/U_Analog_IN/T_sens4: J5.5, R40.2, R49.1
/slave1_of_2/U_Analog_IN/T_sens5: J5.6, R39.2, R50.1
/slave1_of_2/U_Analog_IN/T_sens6: J5.7, R38.2, R51.1
/slave1_of_2/U_Analog_IN/T_sens7: J7.2, R37.2, R52.1
/slave1_of_2/U_Analog_IN/T_sens8: J8.8, R60.2, R61.1
/slave1_of_2/U_Analog_IN/T_sens9: J8.7, R59.2, R62.1
/slave1_of_2/U_Analog_IN/T_sens10: J8.6, R58.2, R63.1
/slave1_of_2/U_Analog_IN/T_sens11: J8.5, R57.2, R64.1
/slave1_of_2/U_Analog_IN/T_sens12: J8.4, R56.2, R65.1
/slave1_of_2/U_Analog_IN/T_sens13: J8.3, R55.2, R66.1
/slave1_of_2/U_Analog_IN/T_sens14: J8.2, R54.2, R67.1
/slave1_of_2/U_Analog_IN/T_sens15: J8.1, R53.2, R68.1
/slave1_of_2/U_Connectors/Cell.0: F4.1, J4.6
/slave1_of_2/U_Connectors/Cell.1: F5.1, J4.2
/slave1_of_2/U_Connectors/Cell.2: F7.1, J4.5
/slave1_of_2/U_Connectors/Cell.3: F8.1, J4.1
/slave1_of_2/U_Connectors/Cell.4: F9.1, J4.4
/slave1_of_2/U_Connectors/Cell.5: F11.1, J3.2
/slave1_of_2/U_Connectors/Cell.6: F12.1, J6.6
/slave1_of_2/U_Connectors/Cell.7: F13.1, J6.3
/slave1_of_2/U_Connectors/Cell.8: F14.1, J6.5
/slave1_of_2/U_Connectors/Cell.9: F15.1, J6.2
/slave1_of_2/U_Connectors/Cell.10: F16.1, J6.4
/slave1_of_2/U_Connectors/Cell.11: F6.1, F17.1, J6.1
/slave1_of_2/U_Connectors/Cell.GND: F3.1, F10.1, J4.3
/slave1_of_2/U_Input_Fuses/Cell_Fused.0: F4.2, IC9.2 (K), Q10.2 (S), R35.1, R101.2, R102.2
/slave1_of_2/U_Input_Fuses/Cell_Fused.1: F5.2, IC7.2 (K), Q7.2 (S), R33.1, R91.2, R92.2
/slave1_of_2/U_Input_Fuses/Cell_Fused.2: F7.2, IC5.2 (K), Q5.2 (S), R31.1, R83.2, R84.2
/slave1_of_2/U_Input_Fuses/Cell_Fused.3: F8.2, IC3.2 (K), Q3.2 (S), R30.1, R75.2, R76.2
/slave1_of_2/U_Input_Fuses/Cell_Fused.4: F9.2, IC13.2 (K), Q1.2 (S), R29.1, R115.2, R116.2
/slave1_of_2/U_Input_Fuses/Cell_Fused.5: F11.2, IC10.2 (K), Q11.2 (S), R28.1, R103.2, R104.2
/slave1_of_2/U_Input_Fuses/Cell_Fused.6: F12.2, IC8.2 (K), Q8.2 (S), R27.1, R93.2, R94.2
/slave1_of_2/U_Input_Fuses/Cell_Fused.7: F13.2, IC6.2 (K), Q6.2 (S), R26.1, R85.2, R86.2
/slave1_of_2/U_Input_Fuses/Cell_Fused.8: F14.2, IC4.2 (K), Q4.2 (S), R25.1, R77.2, R78.2
/slave1_of_2/U_Input_Fuses/Cell_Fused.9: F15.2, IC14.2 (K), Q2.2 (S), R24.1, R117.2, R118.2
/slave1_of_2/U_Input_Fuses/Cell_Fused.10: F16.2, IC11.2 (K), Q12.2 (S), R34.1, R105.2, R106.2
/slave1_of_2/U_Input_Fuses/Cell_Fused.11: F17.2, Q9.2 (S), R32.1
/slave1_of_2/U_Input_Fuses/Cell_Fused.GND: F3.2, IC12.2 (K), R36.1, R113.2, R114.2
/slave1_of_2/U_Passive_Balancing/GLOBAL_BAL_FEEDBACK: C69.1, IC3.3 (E), IC4.3 (E), IC5.3 (E), IC6.3 (E), IC7.3 (E), IC8.3 (E), IC9.3 (E), IC10.3 (E), IC11.3 (E), IC12.3 (E), IC13.3 (E), IC14.3 (E), R119.1, U1.29 (GPIO3)
/slave1_of_2/U_Passive_Balancing/S1: R107.2, U1.25 (S1)
/slave1_of_2/U_Passive_Balancing/S2: R95.2, U1.23 (S2)
/slave1_of_2/U_Passive_Balancing/S3: R87.2, U1.21 (S3)
/slave1_of_2/U_Passive_Balancing/S4: R79.2, U1.19 (S4)
/slave1_of_2/U_Passive_Balancing/S5: R71.2, U1.17 (S5)
/slave1_of_2/U_Passive_Balancing/S6: R108.2, U1.15 (S6)
/slave1_of_2/U_Passive_Balancing/S7: R96.2, U1.13 (S7)
/slave1_of_2/U_Passive_Balancing/S8: R88.2, U1.11 (S8)
/slave1_of_2/U_Passive_Balancing/S9: R80.2, U1.9 (S9)
/slave1_of_2/U_Passive_Balancing/S10: R72.2, U1.7 (S10)
/slave1_of_2/U_Passive_Balancing/S11: R109.2, U1.5 (S11)
/slave1_of_2/U_Passive_Balancing/S12: R97.2, U1.3 (S12)
/slave1_of_2/U_Primary_ADBMS/C0: C41.2, D18.2 (A), R36.2, U1.26 (C0), U2.26 (C0)
/slave1_of_2/U_Primary_ADBMS/C1: C37.2, C40.1, C41.1, D16.2 (A), D18.1 (K), R35.2, U1.24 (C1), U2.24 (C1)
/slave1_of_2/U_Primary_ADBMS/C2: C33.2, C36.1, C37.1, D14.2 (A), D16.1 (K), R33.2, U1.22 (C2), U2.22 (C2)
/slave1_of_2/U_Primary_ADBMS/C3: C31.2, C32.1, C33.1, D13.2 (A), D14.1 (K), R31.2, U1.20 (C3), U2.20 (C3)
/slave1_of_2/U_Primary_ADBMS/C4: C29.2, C30.1, C31.1, D12.2 (A), D13.1 (K), R30.2, U1.18 (C4), U2.18 (C4)
/slave1_of_2/U_Primary_ADBMS/C5: C27.2, C28.1, C29.1, D11.2 (A), D12.1 (K), R29.2, U1.16 (C5), U2.16 (C5)
/slave1_of_2/U_Primary_ADBMS/C6: C25.2, C26.1, C27.1, D10.2 (A), D11.1 (K), R28.2, U1.14 (C6), U2.14 (C6)
/slave1_of_2/U_Primary_ADBMS/C7: C23.2, C24.1, C25.1, D9.2 (A), D10.1 (K), R27.2, U1.12 (C7), U2.12 (C7)
/slave1_of_2/U_Primary_ADBMS/C8: C21.2, C22.1, C23.1, D8.2 (A), D9.1 (K), R26.2, U1.10 (C8), U2.10 (C8)
/slave1_of_2/U_Primary_ADBMS/C9: C19.2, C20.1, C21.1, D7.2 (A), D8.1 (K), R25.2, U1.8 (C9), U2.8 (C9)
/slave1_of_2/U_Primary_ADBMS/C10: C18.1, C19.1, C39.2, D7.1 (K), D17.2 (A), R24.2, U1.6 (C10), U2.6 (C10)
/slave1_of_2/U_Primary_ADBMS/C11: C35.2, C38.1, C39.1, D15.2 (A), D17.1 (K), R34.2, U1.4 (C11), U2.4 (C11)
/slave1_of_2/U_Primary_ADBMS/C12: C34.1, C35.1, D15.1 (K), R32.2, U1.2 (C12), U2.2 (C12)
/slave1_of_2/U_Primary_ADBMS/IN_M1: R4.1, T1.7 (SEC_1), U1.41 (CSB/IMA)
/slave1_of_2/U_Primary_ADBMS/IN_P1: R4.2, T1.9 (SEC_3), U1.42 (SCK/IPA)
/slave1_of_2/U_Primary_ADBMS/OUT_M1: R7.1, T1.10 (SEC_4), U1.47 (IMB)
/slave1_of_2/U_Primary_ADBMS/OUT_P1: R7.2, T1.12 (SEC_6), U1.48 (IPB)
/slave1_of_2/U_Primary_ADBMS/isoSPI_IN+: J1.1, T1.4 (PRI_4)
/slave1_of_2/U_Primary_ADBMS/isoSPI_IN-: J1.2, T1.6 (PRI_6)
/slave1_of_2/U_Primary_ADBMS/isoSPI_OUT+: T1.1 (PRI_1), T4.4 (PRI_4)
/slave1_of_2/U_Primary_ADBMS/isoSPI_OUT-: T1.3 (PRI_3), T4.6 (PRI_6)
/slave1_of_2/U_Primary_ADBMS/prim3V3: C2.1, U1.35 (VREF1)
/slave1_of_2/U_Secondary_ADBMS/IN_M1: R15.1, T2.7 (SEC_1), U2.41 (CSB/IMA)
/slave1_of_2/U_Secondary_ADBMS/IN_P1: R15.2, T2.9 (SEC_3), U2.42 (SCK/IPA)
/slave1_of_2/U_Secondary_ADBMS/OUT_M1: R18.1, T2.10 (SEC_4), U2.47 (IMB)
/slave1_of_2/U_Secondary_ADBMS/OUT_P1: R18.2, T2.12 (SEC_6), U2.48 (IPB)
/slave1_of_2/U_Secondary_ADBMS/isoSPI_IN+: J1.4, T2.4 (PRI_4)
/slave1_of_2/U_Secondary_ADBMS/isoSPI_IN-: J1.3, T2.6 (PRI_6)
/slave1_of_2/U_Secondary_ADBMS/isoSPI_OUT+: T2.1 (PRI_1), T3.4 (PRI_4)
/slave1_of_2/U_Secondary_ADBMS/isoSPI_OUT-: T2.3 (PRI_3), T3.6 (PRI_6)
/slave1_of_2/U_Secondary_ADBMS/sec3v3: C9.1, U2.35 (VREF1)
/slave1_of_2/VBAT+: D2.2 (A), D5.2 (A), F6.2
/slave1_of_2/prim+3V: C3.1, C43.1, R37.1, R38.1, R39.1, R40.1, R41.1, R42.1, R43.1, R44.1, TP1.1, U1.34 (VREF2)
/slave1_of_2/prim+5V: C1.1, C4.1, C17.2, C42.1, C63.1, D1.2 (A), D19.2, F1.1, IC1.8 (VCC), R1.1, R8.1, R9.1, R10.1, R11.1, TP3.1, U1.36 (DTEN), U1.37 (VREG), U1.40 (ISOMD), U4.2 (~RESET), U4.13 (VDD), U7.5
/slave1_of_2/sec+3v: C10.1, C53.1, R53.1, R54.1, R55.1, R56.1, R57.1, R58.1, R59.1, R60.1, TP2.1, U2.34 (VREF2)
/slave1_of_2/sec+5v: C8.1, C11.1, C52.1, C62.1, C68.2, D4.2 (A), D19.1, F2.1, IC2.8 (VCC), R12.1, R19.1, R20.1, R21.1, R22.1, R23.1, TP6.1, U2.37 (VREG), U2.40 (ISOMD), U5.2 (~RESET), U5.13 (VDD), U6.5
/slave2_of_2/EXT_DC_ISO_prim: C112.1, D36.1 (K), D37.1 (A1), L4.1, R147.1, TP15.1
/slave2_of_2/EXT_DC_ISO_sec: C77.1, D21.1 (K), D22.1 (A1), L3.1, R122.1, TP11.1
/slave2_of_2/GND: C70.2, C71.2, C72.2, C73.2, C74.2, C75.2, C76.2, C77.2, C78.2, C79.1, C80.2, C82.2, C84.2, C86.2, C88.2, C90.2, C92.2, C94.2, C96.2, C98.2, C100.2, C102.2, C104.2, C105.2, C106.2, C107.2, C108.2, C109.2, C110.2, C111.2, C112.2, C113.2, C114.1, C115.2, C116.2, C117.1, C118.1, C119.1, C120.1, C121.1, C122.1, C123.1, C124.1, C125.2, C126.2, C127.1, C128.1, C129.1, C130.1, C131.1, C132.1, C133.1, C134.1, C135.2, C136.2, C137.2, C138.2, C141.1, C142.1, C145.1, C146.1, D22.2 (A2), D37.2 (A2), F26.2, IC15.3 (E2), IC15.4 (VSS), IC16.3 (E2), IC16.4 (VSS), J11.8, J11.9, J11.10, J11.11, J11.12, J11.13, J11.14, J13.1, J14.9, J14.10, J14.11, J14.12, J14.13, J14.14, J14.15, J14.16, R121.2, R124.2, R146.2, R149.2, R204.2, TP12.1, TP16.1, U9.30 (V-), U9.31 (V-__1), U9.36 (DTEN), U10.2 (GND), U11.30 (V-), U11.31 (V-__1), U12.2 (GND), U13.14 (GND), U13.15 (A1), U13.16 (A0), U14.14 (GND), U14.15 (A1), U14.16 (A0), U15.2, U16.2, U19.1 (GND), U20.1 (GND)
/slave2_of_2/SCL1: IC16.6 (SCL), R152.2, U11.33 (GPIO5), U13.1 (SCL)
/slave2_of_2/SCL2: IC15.6 (SCL), R127.2, U9.33 (GPIO5), U14.1 (SCL)
/slave2_of_2/SDA1: IC16.5 (SDA), R153.2, U11.32 (GPIO4), U13.3 (SDA)
/slave2_of_2/SDA2: IC15.5 (SDA), R128.2, U9.32 (GPIO4), U14.3 (SDA)
/slave2_of_2/Temp_MUX_prim: C138.1, R238.2, U11.27 (GPIO1)
/slave2_of_2/Temp_MUX_sec: C137.1, R237.2, U9.27 (GPIO1)
/slave2_of_2/U_Analog_IN/OPA_TEMP_prim: U13.8 (D), U16.3
/slave2_of_2/U_Analog_IN/OPA_TEMP_sec: U14.8 (D), U15.3
/slave2_of_2/U_Analog_IN/T_sens0: J11.1, R212.2, R213.1
/slave2_of_2/U_Analog_IN/T_sens1: J11.2, R211.2, R214.1
/slave2_of_2/U_Analog_IN/T_sens2: J11.3, R210.2, R215.1
/slave2_of_2/U_Analog_IN/T_sens3: J11.4, R209.2, R216.1
/slave2_of_2/U_Analog_IN/T_sens4: J11.5, R208.2, R217.1
/slave2_of_2/U_Analog_IN/T_sens5: J11.6, R207.2, R218.1
/slave2_of_2/U_Analog_IN/T_sens6: J11.7, R206.2, R219.1
/slave2_of_2/U_Analog_IN/T_sens7: J13.2, R205.2, R220.1
/slave2_of_2/U_Analog_IN/T_sens8: J14.8, R228.2, R229.1
/slave2_of_2/U_Analog_IN/T_sens9: J14.7, R227.2, R230.1
/slave2_of_2/U_Analog_IN/T_sens10: J14.6, R226.2, R231.1
/slave2_of_2/U_Analog_IN/T_sens11: J14.5, R225.2, R232.1
/slave2_of_2/U_Analog_IN/T_sens12: J14.4, R224.2, R233.1
/slave2_of_2/U_Analog_IN/T_sens13: J14.3, R223.2, R234.1
/slave2_of_2/U_Analog_IN/T_sens14: J14.2, R222.2, R235.1
/slave2_of_2/U_Analog_IN/T_sens15: J14.1, R221.2, R236.1
/slave2_of_2/U_Connectors/Cell.0: F20.1, J10.6
/slave2_of_2/U_Connectors/Cell.1: F21.1, J10.2
/slave2_of_2/U_Connectors/Cell.2: F23.1, J10.5
/slave2_of_2/U_Connectors/Cell.3: F24.1, J10.1
/slave2_of_2/U_Connectors/Cell.4: F25.1, J10.4
/slave2_of_2/U_Connectors/Cell.5: F27.1, J9.2
/slave2_of_2/U_Connectors/Cell.6: F28.1, J12.6
/slave2_of_2/U_Connectors/Cell.7: F29.1, J12.3
/slave2_of_2/U_Connectors/Cell.8: F30.1, J12.5
/slave2_of_2/U_Connectors/Cell.9: F31.1, J12.2
/slave2_of_2/U_Connectors/Cell.10: F32.1, J12.4
/slave2_of_2/U_Connectors/Cell.11: F22.1, F33.1, J12.1
/slave2_of_2/U_Connectors/Cell.GND: F19.1, F26.1, J10.3
/slave2_of_2/U_Input_Fuses/Cell_Fused.0: F20.2, IC23.2 (K), Q22.2 (S), R143.1, R186.2, R187.2
/slave2_of_2/U_Input_Fuses/Cell_Fused.1: F21.2, IC21.2 (K), Q19.2 (S), R141.1, R176.2, R177.2
/slave2_of_2/U_Input_Fuses/Cell_Fused.2: F23.2, IC19.2 (K), Q17.2 (S), R139.1, R168.2, R169.2
/slave2_of_2/U_Input_Fuses/Cell_Fused.3: F24.2, IC17.2 (K), Q15.2 (S), R138.1, R160.2, R161.2
/slave2_of_2/U_Input_Fuses/Cell_Fused.4: F25.2, IC27.2 (K), Q13.2 (S), R137.1, R200.2, R201.2
/slave2_of_2/U_Input_Fuses/Cell_Fused.5: F27.2, IC24.2 (K), Q23.2 (S), R136.1, R188.2, R189.2
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

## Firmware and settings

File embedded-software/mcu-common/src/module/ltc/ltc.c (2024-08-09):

/**
 *
 * @copyright &copy; 2010 - 2021, Fraunhofer-Gesellschaft zur Foerderung der
 *  angewandten Forschung e.V. All rights reserved.
 *
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
 * We kindly request you to use one or more of the following phrases to refer
 * to foxBMS in your hardware, software, documentation or advertising
 * materials:
 *
 * &Prime;This product uses parts of foxBMS&reg;&Prime;
 *
 * &Prime;This product includes parts of foxBMS&reg;&Prime;
 *
 * &Prime;This product is derived from foxBMS&reg;&Prime;
 *
 */

/**
 * @file    ltc.c
 * @author  foxBMS Team
 * @date    01.09.2015 (date of creation)
 * @ingroup DRIVERS
 * @prefix  LTC
 *
 * @brief   Driver for the LTC monitoring chip.
 *
 */

/*================== Includes =============================================*/
#include "ltc.h"

#include "database.h"
#include "diag.h"
#include "ltc_pec.h"
#include "os.h"
#include "slaveplausibility.h"

/*================== Macros and Definitions ===============================*/

/**
 * TI port expander register addresses
 *
 */

#define LTC_PORT_EXPANDER_TI_INPUT_REG_ADR    0x00
#define LTC_PORT_EXPANDER_TI_OUTPUT_REG_ADR   0x01
#define LTC_PORT_EXPANDER_TI_CONFIG_REG_ADR   0x03

/**
 * LTC COMM definitions
 */

#define LTC_ICOM_START              0x60
#define LTC_ICOM_STOP               0x10
#define LTC_ICOM_BLANK              0x00
#define LTC_ICOM_NO_TRANSMIT        0x70
#define LTC_FCOM_MASTER_ACK         0x00
#define LTC_FCOM_MASTER_NACK        0x08
#define LTC_FCOM_MASTER_NACK_STOP   0x09

#define LTC_MAX_SUPPORTED_CELLS         12

/**
 * Saves the last state and the last substate
 */
#define LTC_SAVELASTSTATES()    ltc_state.laststate = ltc_state.state; \
                                ltc_state.lastsubstate = ltc_state.substate

#if BS_NR_OF_MODULES != 0

/*================== Constant and Variable Definitions ====================*/

static uint8_t ltc_used_cells_index = 0;

static DATA_BLOCK_CELLVOLTAGE_s ltc_cellvoltage;
static DATA_BLOCK_CELLTEMPERATURE_s ltc_celltemperature;
static DATA_BLOCK_MINMAX_s ltc_minmax;
static DATA_BLOCK_BALANCING_FEEDBACK_s ltc_balancing_feedback;
static DATA_BLOCK_USER_MUX_s ltc_user_mux;
static DATA_BLOCK_BALANCING_CONTROL_s ltc_balancing_control;
static DATA_BLOCK_SLAVE_CONTROL_s ltc_slave_control;
static DATA_BLOCK_ALLGPIOVOLTAGE_s ltc_allgpiovoltage;
static DATA_BLOCK_OPENWIRE_s ltc_openwire;
static uint16_t ltc_openwire_pup_buffer[BS_NR_OF_BAT_CELLS];
static uint16_t ltc_openwire_pdown_buffer[BS_NR_OF_BAT_CELLS];
static int32_t ltc_openwire_delta[BS_NR_OF_BAT_CELLS];

static LTC_ERRORTABLE_s LTC_ErrorTable[LTC_N_LTC];  /* init in LTC_ResetErrorTable-function */


static LTC_STATE_s ltc_state = {
    .timer                   = 0,
    .statereq                = LTC_STATE_NO_REQUEST,
    .state                   = LTC_STATEMACH_UNINITIALIZED,
    .substate                = 0,
    .laststate               = LTC_STATEMACH_UNINITIALIZED,
    .lastsubstate            = 0,
    .adcModereq              = LTC_ADCMODE_FAST_DCP0,
    .adcMode                 = LTC_ADCMODE_FAST_DCP0,
    .adcMeasChreq            = LTC_ADCMEAS_UNDEFINED,
    .adcMeasCh               = LTC_ADCMEAS_UNDEFINED,
    .numberOfMeasuredMux     = 32,
    .triggerentry            = 0,
    .ErrRetryCounter         = 0,
    .ErrRequestCounter       = 0,
    .VoltageSampleTime       = 0,
    .muxSampleTime           = 0,
    .commandDataTransferTime = 3,
    .commandTransferTime     = 3,
    .gpioClocksTransferTime  = 3,
    .muxmeas_seqptr          = NULL_PTR,
    .muxmeas_seqendptr       = NULL_PTR,
    .muxmeas_nr_end          = 0,
    .first_measurement_made  = FALSE,
    .ltc_muxcycle_finished   = E_NOT_OK,
    .check_spi_flag          = FALSE,
    .balance_control_done     = FALSE,
};

static const uint8_t ltc_cmdDummy[1]={0x00};
static const uint8_t ltc_cmdWRCFG[4]={0x00, 0x01, 0x3D, 0x6E};
static const uint8_t ltc_cmdWRCFG2[4]={0x00, 0x24, 0xB1, 0x9E};

static const uint8_t ltc_cmdRDCVA[4] = {0x00, 0x04, 0x07, 0xC2};
static const uint8_t ltc_cmdRDCVB[4] = {0x00, 0x06, 0x9A, 0x94};
static const uint8_t ltc_cmdRDCVC[4] = {0x00, 0x08, 0x5E, 0x52};
static const uint8_t ltc_cmdRDCVD[4] = {0x00, 0x0A, 0xC3, 0x04};
static const uint8_t ltc_cmdRDCVE[4] = {0x00, 0x09, 0xD5, 0x60};
static const uint8_t ltc_cmdRDCVF[4] = {0x00, 0x0B, 0x48, 0x36};
static const uint8_t ltc_cmdWRCOMM[4] = {0x07, 0x21, 0x24, 0xB2};
static const uint8_t ltc_cmdSTCOMM[4] = {0x07, 0x23, 0xB9, 0xE4};
static const uint8_t ltc_cmdRDCOMM[4] = {0x07, 0x22, 0x32, 0xD6};
static const uint8_t ltc_cmdRDAUXA[4] = {0x00, 0x0C, 0xEF, 0xCC};
static const uint8_t ltc_cmdRDAUXB[4] = {0x00, 0x0E, 0x72, 0x9A};
static const uint8_t ltc_cmdRDAUXC[4] = {0x00, 0x0D, 0x64, 0xFE};
static const uint8_t ltc_cmdRDAUXD[4] = {0x00, 0x0F, 0xF9, 0xA8};

/* static const uint8_t ltc_cmdMUTE[4] = {0x00, 0x28, 0xE8, 0x0E};                    !< MUTE discharging via S pins */
/* static const uint8_t ltc_cmdUNMUTE[4] = {0x00, 0x29, 0x63, 0x3C};                  !< UN-MUTE discharging via S pins */

/* LTC I2C commands */
/* static const uint8_t ltc_I2CcmdDummy[6] = {0x7F, 0xF9, 0x7F, 0xF9, 0x7F, 0xF9};      !< dummy command (no transmit) */

static const uint8_t ltc_I2CcmdTempSens0[6] = {0x69, 0x08, 0x00, 0x09, 0x7F, 0xF9};  /*!< sets the internal data pointer of the temperature sensor (address 0x48) to 0x00 */
static const uint8_t ltc_I2CcmdTempSens1[6] = {0x69, 0x18, 0x0F, 0xF0, 0x0F, 0xF9};  /*!< reads two data bytes from the temperature sensor */

static const uint8_t ltc_I2CcmdPortExpander1[6] = {0x64, 0x18, 0x0F, 0xF9, 0x7F, 0xF9};  /*!< reads one data byte from the port expander */

/* Cells */
static const uint8_t ltc_cmdADCV_normal_DCP0[4] = {0x03, 0x60, 0xF4, 0x6C};        /*!< All cells, normal mode, discharge not permitted (DCP=0)    */
static const uint8_t ltc_cmdADCV_normal_DCP1[4] = {0x03, 0x70, 0xAF, 0x42};        /*!< All cells, normal mode, discharge permitted (DCP=1)        */
static const uint8_t ltc_cmdADCV_filtered_DCP0[4] = {0x03, 0xE0, 0xB0, 0x4A};      /*!< All cells, filtered mode, discharge not permitted (DCP=0)  */
static const uint8_t ltc_cmdADCV_filtered_DCP1[4] = {0x03, 0xF0, 0xEB, 0x64};      /*!< All cells, filtered mode, discharge permitted (DCP=1)      */
static const uint8_t ltc_cmdADCV_fast_DCP0[4] = {0x02, 0xE0, 0x38, 0x06};          /*!< All cells, fast mode, discharge not permitted (DCP=0)      */
static const uint8_t ltc_cmdADCV_fast_DCP1[4] = {0x02, 0xF0, 0x63, 0x28};          /*!< All cells, fast mode, discharge permitted (DCP=1)          */
static const uint8_t ltc_cmdADCV_fast_DCP0_twocells[4] = {0x02, 0xE1, 0xb3, 0x34}; /*!< Two cells (1 and 7), fast mode, discharge not permitted (DCP=0) */
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

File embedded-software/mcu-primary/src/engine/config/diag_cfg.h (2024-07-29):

/**
 *
 * @copyright &copy; 2010 - 2021, Fraunhofer-Gesellschaft zur Foerderung der
 *  angewandten Forschung e.V. All rights reserved.
 *
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
 * We kindly request you to use one or more of the following phrases to refer
 * to foxBMS in your hardware, software, documentation or advertising
 * materials:
 *
 * &Prime;This product uses parts of foxBMS&reg;&Prime;
 *
 * &Prime;This product includes parts of foxBMS&reg;&Prime;
 *
 * &Prime;This product is derived from foxBMS&reg;&Prime;
 *
 */

/**
 * @file    diag_cfg.h
 * @author  foxBMS Team
 * @date    09.11.2015 (date of creation)
 * @ingroup ENGINE_CONF
 * @prefix  DIAG
 *
 * @brief   Diagnostic module configuration header
 *
 * In this header filer are the different diagnosis channel
 * defines assigned to different diagnosis IDs.
 *
 * Furthermore are the diagnosis error log settings be configured here..
 */

#ifndef DIAG_CFG_H_
#define DIAG_CFG_H_

/*================== Includes ===============================================*/
#include "general.h"

#include "batterysystem_cfg.h"

/*================== Macros and Definitions =================================*/
#define DIAG_ERROR_SENSITIVITY_HIGH         (0)    /* logging at first event */
#define DIAG_ERROR_SENSITIVITY_MID          (5)    /* logging at fifth event */
#define DIAG_ERROR_SENSITIVITY_LOW          (10)   /* logging at tenth event */

#define DIAG_ERROR_VOLTAGE_SENSITIVITY_MSL      (500)   /*!< MSL level for event occurrence if over/under voltage event   */
#define DIAG_ERROR_VOLTAGE_SENSITIVITY_RSL      (500)   /*!< RSL level for event occurrence if over/under voltage event   */
#define DIAG_ERROR_VOLTAGE_SENSITIVITY_MOL      (500)   /*!< MOL level for event occurrence if over/under voltage event   */

#define DIAG_ERROR_TEMPERATURE_SENSITIVITY_MSL  (500)   /*!< MSL level for event occurrence if over/under temperature event    */
#define DIAG_ERROR_TEMPERATURE_SENSITIVITY_RSL  (500)   /*!< RSL level for event occurrence if over/under temperature event    */
#define DIAG_ERROR_TEMPERATURE_SENSITIVITY_MOL  (500)   /*!< MOL level for event occurrence if over/under temperature event    */

#define DIAG_ERROR_CURRENT_SENSITIVITY_MSL      (500)   /*!< MSL level for event occurrence if over/under current event        */
#define DIAG_ERROR_CURRENT_SENSITIVITY_RSL      (500)   /*!< RSL level for event occurrence if over/under current event        */
#define DIAG_ERROR_CURRENT_SENSITIVITY_MOL      (500)   /*!< MOL level for event occurrence if over/under current event        */

#define DIAG_ERROR_SLAVE_TEMP_SENSITIVITY_MSL   (500)   /*!< MSL level for event occurrence if slave PCB temperature event     */
#define DIAG_ERROR_SLAVE_TEMP_SENSITIVITY_RSL   (500)   /*!< RSL level for event occurrence if slave PCB temperature event     */
#define DIAG_ERROR_SLAVE_TEMP_SENSITIVITY_MOL   (500)   /*!< MOL level for event occurrence if slave PCB temperature event     */

#define DIAG_ERROR_LTC_PEC_SENSITIVITY          (5)
#define DIAG_ERROR_LTC_MUX_SENSITIVITY          (5)
#define DIAG_ERROR_LTC_SPI_SENSITIVITY          (5)

#define DIAG_ERROR_CAN_TIMING_SENSITIVITY       (100)
#define DIAG_ERROR_CAN_TIMING_CC_SENSITIVITY    (100)
#define DIAG_ERROR_CAN_SENSOR_SENSITIVITY       (100)

#define DIAG_ERROR_MAIN_PLUS_SENSITIVITY        (50)
#define DIAG_ERROR_MAIN_MINUS_SENSITIVITY       (50)
#define DIAG_ERROR_PRECHARGE_SENSITIVITY        (50)

#define DIAG_ERROR_INTERLOCK_SENSITIVITY        (10)

#define DIAG_ERROR_INSULATION_SENSITIVITY       (30)

#define DIAG_ERROR_PLAUSIBILITY_PACK_SENSITIVITY    (100)

/** Number of errors that can be logged */
#define DIAG_FAIL_ENTRY_LENGTH              (50)

/** Maximum number of the same errors that are logged */
#define DIAG_MAX_ENTRIES_OF_ERROR           (5)

/** Number of contactor errors that are logged */
#define DIAG_FAIL_ENTRY_CONTACTOR_LENGTH    (50)
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

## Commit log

2024-06-05 V1.7_Beta
    longer wait for interlock to wait before checking state again
    [sof.xlsx]
2024-06-08 V1.7 Beta 2
    added open wire periodic check, and can messages
2024-06-10 V1.7 Beta 3
    version at end of 2nd rolling try
    other commented out things for error ingnoring
    [batterysystem_cfg.h]
2024-06-11 V1.7 Beta 4
    CRC and MUX errors do not put bms in error
2024-07-03 tous les messges s'envoient maintenant
    l'erreur vennais du temps avant d'envoyer le premier message qui doit etre inferieur du temps auquel l'on envoi le message periodiquement
2024-07-04 temps de delanhements ammeiloré
    en cas d'erreur les contacteurs s'ouvernt plus rapidement
2024-07-10 new changes
    not working when driving and problem with crc error still here
    [batterycell_cfg.h, batterysystem_cfg.h, can_cfg.c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]
2024-07-11 les contacteurs se ferment completement
    crc check +10 fois pour erreur correcte
    [ltc.c, ltc_cfg.h]
2024-07-31 minor changes
    changed some balancing values
    changed so that default mode after bootup is standby instead of idle
    [BMS-Master.kicad_pcb]

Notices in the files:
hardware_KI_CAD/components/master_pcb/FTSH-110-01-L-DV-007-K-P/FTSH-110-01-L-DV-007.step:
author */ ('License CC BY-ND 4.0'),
